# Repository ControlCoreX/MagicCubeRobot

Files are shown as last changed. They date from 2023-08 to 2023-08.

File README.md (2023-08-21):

# MagicCubeRobot
自己做的一个全自动解魔方装置. (下了大力气, 花了大价钱)

我的邮箱地址: TwithZ@163.com, 欢迎讨论交流!

演示视频地址: [演示视频](https://www.bilibili.com/video/BV1zj411979p/?vd_source=939818502857687a4a334c7a40d2c98a).

## 1. 整体简介
这是我做的第一个完整度较高的项目, 整体分为3个部分: 上位机, 下位机, 机械结构.
1. 上位机: (树莓派+上位机)
   1. 使用的技术: 树莓派4B(8GB); 使用opencv进行图像处理; 全部使用C++语言编写; 使用g++编译器构建; 使用CMake工具管理工程; 使用git进行版本控制; 使用POSIX pthread线程库进行多线程设计; 使用了WiringPi库控制串口(但实际大多是使用的都是Linux的系统调用进行数据读写); 没有使用GUI, 采用了CLI的方式与用户交互(虽然但是, 经过我的设计, 操作起来也非常方便); 还用Qt编写了一个上位机(仅用于中继, 它的功能后面会介绍), 其中使用了winsocket进行本机网络通信.
   2. 负责的功能: 负责与用户的交互, 图像的采集, 魔方描述字符串的生成, 与开源解魔方软件网络通信, 与下位机通信.
2. 下位机:
   1. 使用的技术: STM32F407+FreeRTOS.
   2. 负责的功能: 接收上位机传来的指令, 并控制步进电机运动.
3. 机械部分: SolidWorks, 零件都是在网上加工的, 使用的材料有CNC铝加工(只用了一小点, 奈何实在是太贵了), 3D打印树脂, 尼龙, 亚克力板, 不锈钢冲压工艺. (后面这些都是妥协的. 由于第一次做机加工这种事, 前期没有料想到CNC铝加工这么贵, 所以最开始计划的是全部都是用CNC, 后来发现太贵了, 才一点一点妥协, 从铝变成了3D打印塑料, 变成了冲压的不锈钢, 变成了亚克力板. 不过我感觉这也是一个成长过程吧, 以后做产品的话, 在机加工这方面也肯定是要根据成本来选择加工工艺的啊)

## 2. 软件架构介绍
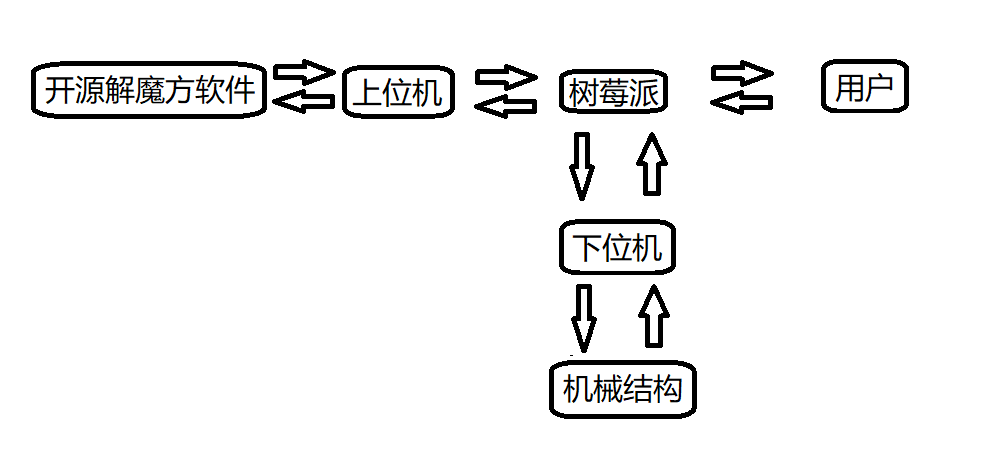
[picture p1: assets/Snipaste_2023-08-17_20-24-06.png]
整体架构图

**1. 架构图说明**: 整体架构关系图如上图所示, 在操作过程中, 用户只需要通过鼠标键盘与树莓派进行交互就可以了, 极大简化了操作, 在设计时我是有意设置成这样的, 用户完全不用操作STM32, <u>我相当于把STM32当做了树莓派的一个从设备.</u> 系统上电之后(就只有一个开关), 用户所需做的就是操作鼠标和键盘. 用户把需要的动作以指令的形式输入给树莓派, 树莓派会将会根据指令控制STM32, 进而控制机械机构来执行对应动作.

**2. 工作流程**: 系统初始化 > 树莓派采集图像 > 通过算法识别出魔方6个面, 共计54个色块的颜色 > 树莓派根据颜色生成描述魔方色块和方位信息的字符串 > 将字符串通过串口发送给上位机 > 上位机通过网络将该字符串发送给开源解魔方软件, 该软件会自动给出魔方还原步骤, 并返回给上位机 > 上位机将还原步骤发送给树莓派 > 树莓派将还原步骤发送给下位机 > 下位机根据还原步骤解析生成实际控制电机的结构体数组 > STM32控制机械结构全自动完成魔方还原.

**3. 上位机软件设计**: 使用树莓派4B, 采用POSIX多线程. 使用opencv进行图像处理和颜色识别. 下面只讲几个比较重要的点吧.
1. 实时识别. 颜色识别是在视频流中直接识别的, 而不是先拍摄图像, 后进行识别. 这样反馈通路的延迟小, 便于快速获得识别结果. 程序在视频流中直接显示识别结果, 当识别结果正确时, 用户只需要敲一下键盘即可去识别魔方的下一个面.
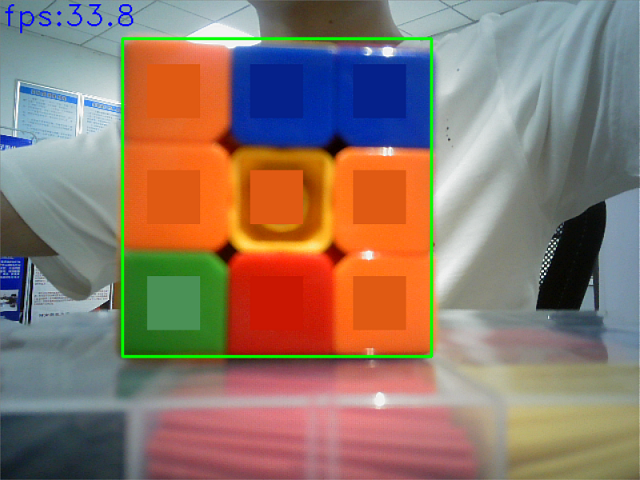
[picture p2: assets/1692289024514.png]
实时识别
   
2. 颜色识别算法在**BGR色彩空间**中完成, 使用颜色距离来判断两种颜色的接近程度, 从而判断出目标色块的颜色. 因为一种彩色有BGR共3个通道, 也就是3个分量, 如果分别以BGR3个分量为坐标轴, 那么它们所能形成的所有颜色, 在空间中就可以形成一个处于第一卦限的正方体(离散的). 那么以这种视角, 每一种颜色在空间中也就是一个点, 那么两种颜色的接近程度就可以用这两个点之间的距离来衡量, 距离近表示两种颜色很接近, 距离远表示两种颜色差异很大. (注: 这里这种距离我使用的是欧氏距离, 具体原因我目前无法解释, 但是效果很好; 还有一种距离叫曼哈顿距离, 我没有试, 不知道效果会怎么样). 公式如下:
公式
3. 在图像领域一个非常影响软件性能的因素就是光照, 在这个项目的颜色识别中也不例外, 我在设计中非常要注意的一个点就是对于光照的抗干扰能力要强. 为此我设计了一个debug线程, 专门用于调整bgr的阈值, 因为识别颜色主要就靠这些阈值来进行的. 不同于一般的手动调整阈值的方法, 我在设计时着重考虑了易用性, 即**用户友好性friendly**. 当某个颜色识别不准确时, 只需按下一个键便会自动创建一个debug线程, 然后在这里用户只需要手动指定一下识别不准确的颜色, 然后程序会自动计算该处的bgr值, 然后以计算得到的值来作为阈值. (实际测试, 这种方法效果很好)
4. 设计实现了一个功能类似shell的软件. 实现的效果为: 用户可以在树莓派的terminal中输入一个函数名, 并带上参数, 然后回车, 单片机上就可以执行同名的函数, 并使用在terminal输入的参数(且参数可定制, 默认支持3个参数). 即我可以在单片机运行时手动让其执行某个函数. 这种设计非常方便调试!!! (还有种**分布式**的概念在里面, 树莓派上的线程, 单片机上的线程, 都当做是同等的线程, 只不过是跑在不同的设备上的而已, 我在用的时候直接就把单片机上的线程当做了树莓派上的线程, 因为使用起来在用户看来没什么两样, 中间那一层对用户来说是**透明的**)

**4. 下位机软件设计**: 采用了FreeRTOS实时操作系统, 采用多线程设计, 在软件编写上比裸机要更容易一些. 在该项目中我共使用了4个线程, 分别是: LED状态灯线程`status_led_task`, 限位开关扫描线程`limit_task`, 命令处理线程`cmd_proc_task`, 数据处理线程`data_proc_task`.
1. LED状态灯线程就是用于控制指示灯的亮灭(线程的优先级很低). 在实际产品中, 指示灯的设置非常重要, 它可以用于判断系统是否工作正常, 对于软件调试非常重要.
2. 限位开关扫描线程, 它就是用于扫描限位开关状态的, 因为使用的是步进电机, 并不是闭环的伺服电机, 所以需要使用限位开关来设定初始位置, 再假定步进电机不丢步, 近似认为其是一个闭环系统. 本项目中限位开关的扫描频率为100Hz(最大为), 周期10ms, 要根据滑轨的速度来调节该扫描频率, 过快浪费系统资源, 过慢起不到效果.
3. 命令处理线程和数据处理线程, 在树莓派中我设计了两个程序, 一个是主要的程序, 用于图像识别和解魔方, 还有一个程序时专门用于调试的, 其位置在`./树莓派部分/MagicCubeRobot/manual_mode`文件夹下, 见名知意, 即手动模式, 也就是说用户可以通过键盘来控制机械结构的运动, 它跟用于图像识别的程序对STM32的控制是独立的, 所以我在这里就设计了两个线程来分别接收这两个程序对STM32的控制, 但是使用的是同一套通信协议(这个后面讲), 数据处理线程用于处理图像识别程序发来的数据, 命令处理线程用于处理手动控制程序发来的数据. 下面讲一下实现细节:
   - 由于通过树莓派发来的数据都并非是单个字节的, 而是很大一长串, 而且数据的长度还是不确定的(如魔方还原步骤的长短可能不同), 所以这就涉及到串口不定长数据的接收, 关于不定长数据的接收有很多方式, 其中正点原子的方式我感觉不是很好, 至少不是专业的方法, 它是用串口接收中断, 来一个字节就接收一个字节, 最后拼到一块. 我觉得这种方法有一个很大的缺点就是浪费资源, 因为用的是接收中断, 那如果接收的字节数非常多, 那就要中断很多次, 而且中断频率也是很高的, 因为来一个字节就要接收一次(如果波特率是115200的话, 中断频率是可以计算出来的), 而我采用的又是RTOS, 调度器才1ms中断一次, 这导致了在接收数据时, 大部分时间单片机都卡在串口接收中断里, 这很不专业. 所以我觉得这种使用串口接收中断来接收不定长数据的方式只适合做简单的应用, 不适合正规生产中. 在这里我使用的是**串口空闲中断+DMA**的方式, 这种方式高效, 不需要CPU参与数据搬运.
   - 由于数据有两个用途: 数据或命令. 所以我需要在数据包中有一个标识符来标记这个数据包是数据还是命令. 为此我设计了一个协议格式. 如下:
     ```c
     typedef struct
     {
          uint8_t  head;//!< 帧头
	      uint8_t  type;//!< 类型标识符
	      uint16_t len;//!< 数据长度
	      uint8_t  data[USART2_DMA_RECV_BUF_SIZE - 4U];//!< 数据域
     }pack_t;
     ```
     树莓派上的两个程序在向单片机发送数据时都使用这种数据包, 所以单片机就可以根据type成员来判断接收到的是数据还是命令, 从而对数据进行不同的解析, 交给不同的线程去处理.
   - 单片机串口空闲中断接收到一个数据包中断一次, 然后通过type成员执行不同的操作, 进而唤醒不同的线程(当没有接收到数据时, 对应的线程都是阻塞状态的), 进行不同的处理.
   - 还有一些别的细节, 如两种数据的种类是不一样的, 命令时数据类型是`uint32_t`型的, 而数据时数据类型是`uint8_t`类型的, 为了方便, 我在设计时将数据传输流规定为了使字节流, 所以如果传输的是命令, 还要根据机器的**大小端**进行4个byte拼接为一个`uint32_t`.

**5. 一些软件设计细节!!!**: (代码强迫症...)
1. 代码命名规范. 命名使用Unix的风格, 即全部小写, 以下划线分隔; 对于常用单词的缩写也有规定, 对于同一个单词, 不允许使用不同的缩写. 比如length缩写就为len, command的缩写久违cmd, 所有地方都保持统一. 这种做法有人可能认为是强迫症, 但我认为"不乱起名", "名称保持统一"在软件开发中是一个好习惯, 不至于引起迷惑!!!
2. 注释规范. (符合doxygen注释规范, 便于自动生成文档)
   ```c
   //! 单行行首注释.
   func_bar();//!< 单行行尾注释.
   /*!
    * 多行注释.
    * 多行注释.
    */
3. Terminal中输出的信息为彩色, 不同level的log用不同颜色的输出表示. 典型的就是绿色表示成功, 红色表示失败. 我还使用了蓝色表示较为重要的提示.
4. 统统采用多线程设计. 我觉得这应该是以后的主流, 裸跑不太好.

## 3. 硬件部分
这一部分就只是设计了一个转接板, 主要是为了方便连线, 不让走线太凌乱, 因为一共使用了11个步进电机, 1个舵机, 4个限位开关, 一共大约是125根线, 如果都直接连到核心板上多少有点难看, 而且还不稳定, 再者我要以做产品的标准来要求自己, 所以我弄了一个转接板, 通过接线端子来吧这些线引出去, 最终效果很好, 也没有显得很凌乱.
![转接板图片](./assets/1692288660302.jpg)

## 4. 机械部分
![3维模型](./assets/1692289251094.jpg)
这一部分也是我在这个项目中花费精力最大的一部分, 由于之前没有做过机加工的经验, SolidWorks也是现学现卖, 对于很多东西都不懂, 中间也踩了很多坑, 在这里感谢实验室王老师的资金支持!!!

在设计机械机构使我的主要目标就是要实现全自动, 之前一代解魔方机器是使用了4个摄像头, 这里我设计了一套机械装置实现了仅使用一个摄像头就可以实现对魔方6个面的图像采集. 如上图中红圈中的结构.

为了保证水平方向4个拧手在向中心运动时的一致性, 我还设计了一套联动机构, 通过同步轮和同步带实现水平方向4个电机同时到达中心位置.

总之吧, 在设计上我注意了很多细节, 这里就不一一说了, 说多了都是泪......

---

2023年8月18日00:31:47

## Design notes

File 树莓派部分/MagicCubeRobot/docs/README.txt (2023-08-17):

约定:
    通道顺序使用bgr, 而非rgb. 在命名中也使用了bgr.
    对于那种可以使用一维数组, 也可以用二维数组表示的数据. 约定:
        如果选择用一维数组来表示, 则数组名使用复数.
        如果选择用二维数组来表示, 则数组名使用单数.
    一共分为3个线程:
        1. 进行色块识别的线程叫 video thread.
        2. 获取各种颜色的bgr值得线程叫 debug thread.
        3. 与下位机进行通信的线程叫 com thread.
    标记都用绿色.
    
由于很多情况下, 对象都并非单纯的变量, 那么通过函数返回值返回这种对象就比较不方便.
另外为了形式上的统一, 规定: 尽量让函数的返回值都是void, 数据的传入和传出都通过参数完成.
而且对于需要传出数据的参数, 使用"引用"的语法, 而不适用"指针"的语法.

关于函数形参的顺序的约定: 传入参数在前, 传出参数在后.

在终端中的提示的颜色:
    错误: 红色加粗
    成功: 绿色加粗
    一般提示: 白色加粗.
    稍重要提示: 蓝色加粗.

命名规范:
    calculate 简写为 calc
    sample    简写为 samp

名词解释:
    roi表示的是摄像头拍到的画面中, 魔方所在的区域, 认为是roi.
    samp表示的是判定颜色时, 参与计算的区域.

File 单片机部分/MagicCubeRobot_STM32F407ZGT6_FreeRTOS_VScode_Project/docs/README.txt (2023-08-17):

/*!
 * @file: README.txt
 * @author: 屠文博-自卓201-201404010126
 * @date: 2023年5月17日20:53:26
 * @brief:  1. 一些硬件资源分配信息.
 *          2. 注意事项.
 *          3. 一些规范.
 */

解魔方机器人单片机端资源分配(2023年4月4日16:17:47)

控制步进电机使用 TIM3, CH1, PA6
DMA使用的是 USART2, PA2, PA3
控制舵机使用 TIM4, CH1, PD12

有一个控制步进电机使能与否的按钮, 因为使能, 所有电机可以同时使能, 同时失能, 要是所有11
个电机全部都用一个引脚控制的话, 那得很多引脚, 鉴于此, 直接用地线和vcc来控制使能失能.
而方向引脚每个电机用一个引脚控制.

步进电机的方向表示, 0表示顺时针, 1表示逆时针.
大部分电机的细分调的都是400个脉冲转一圈. 有些因为速度或其他的原因不是这样的.
单片机每秒产生800个脉冲. 如果是400个一圈的话, 则转速就是1秒转2圈.

一个函数前加了static表示这个函数只希望在本文件中使用, 不需要在外部使用. 类似文件私有的函数.

注释采用Doxygen规范:
    单行注释:   1. 该行中仅有注释:
                    //! 这是注释.
                    this is code;

                2. 在代码后注释:
                    this is code;//!< 这是注释.
    多行注释:   /*!
                * 1. this is comment.
                * 2. this is comment.
                * 3. this is comment.
                */

这是一个vscode工程, 需要先搭建一下vscode开发STM32的环境.

在注释中线程跟任务不作区分.

单词的缩写标准跟上位机一样.

编译程序只需要在命令行里输入make命令并回车即可.
下载程序只需要在命令行里输入make download命令并回车即可. (下载程序时一般第一次下不进去, 这时候拔插一下ST-Link再下就能下进去了. 我也不知道为啥, 还没有去认真解决它)

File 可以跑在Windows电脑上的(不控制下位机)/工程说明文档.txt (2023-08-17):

就跟建VS的opencv工程差不多, 先建一个opencv的工程, 这里面用的opencv3.4.2
因为要用网络通信, 需要在附加依赖项中多加一个ws2_32.lib
因为使用了winsocket和opencv, 里面的命名空间有干扰, 如果不做处理的话, 编译会报错
说"ACCESS_MASK"不明确符号, 这时候需要把"using namespace cv;"这一句给去掉,
然后把所有cv命令空间的东西, 使用cv::这种方式搞一下, 然后就不报错了.

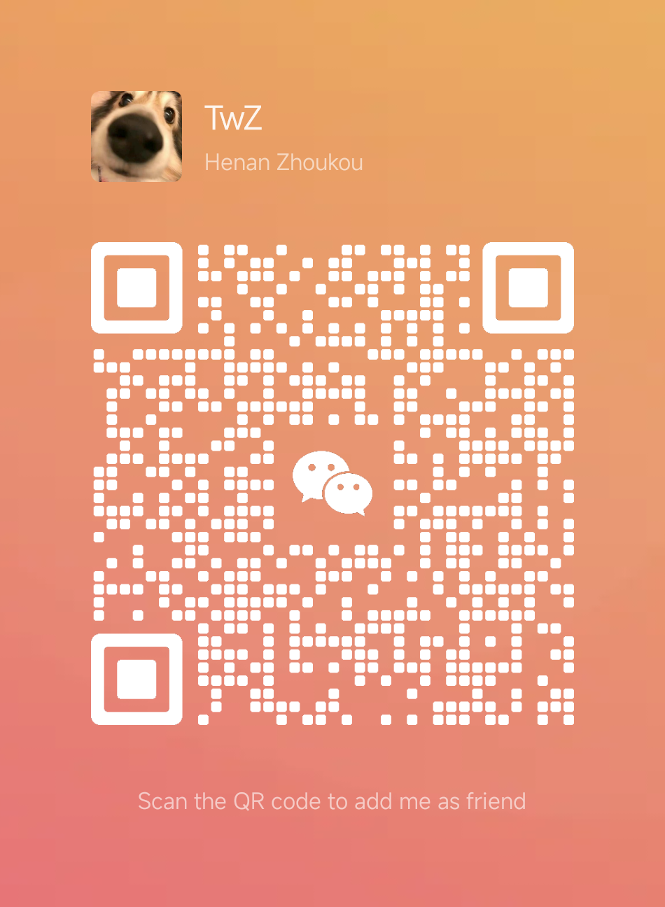
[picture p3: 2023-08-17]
assets/wechat.png

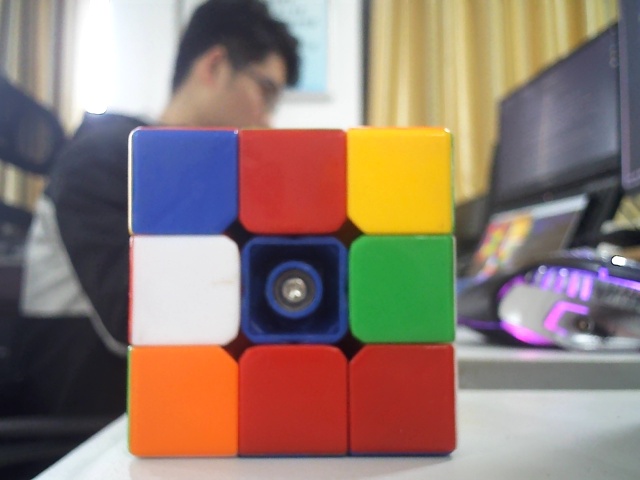
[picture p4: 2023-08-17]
树莓派部分/MagicCubeRobot/picture/six-color.jpg

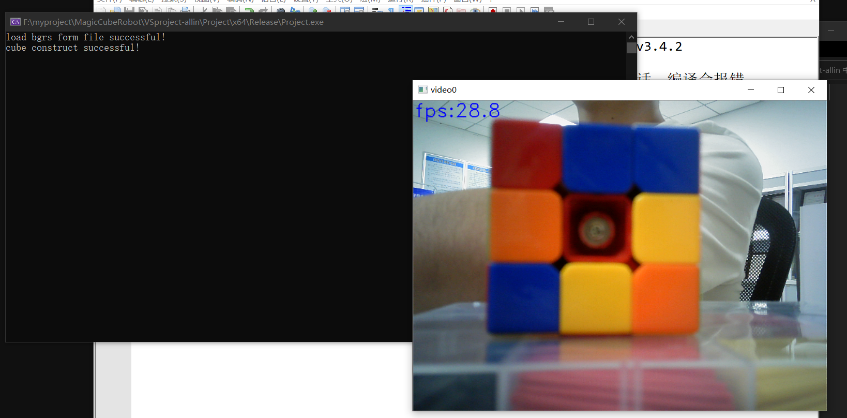
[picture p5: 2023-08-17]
可以跑在Windows电脑上的(不控制下位机)/示例图片/Snipaste_2023-06-06_16-59-30.png

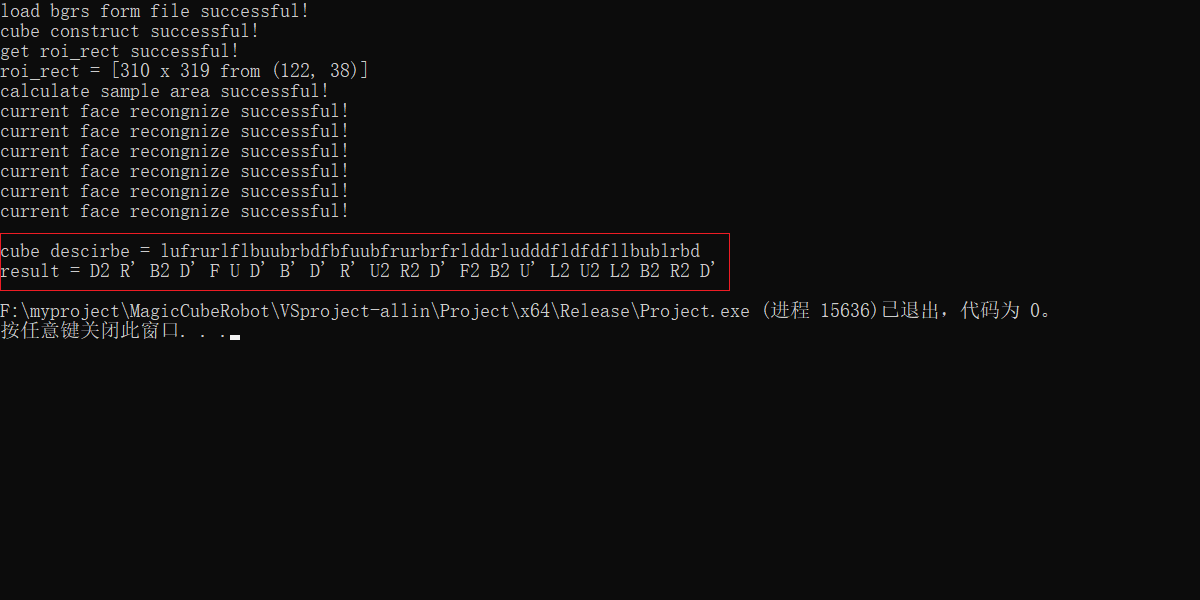
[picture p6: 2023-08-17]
可以跑在Windows电脑上的(不控制下位机)/示例图片/Snipaste_2023-06-06_17-02-21.png

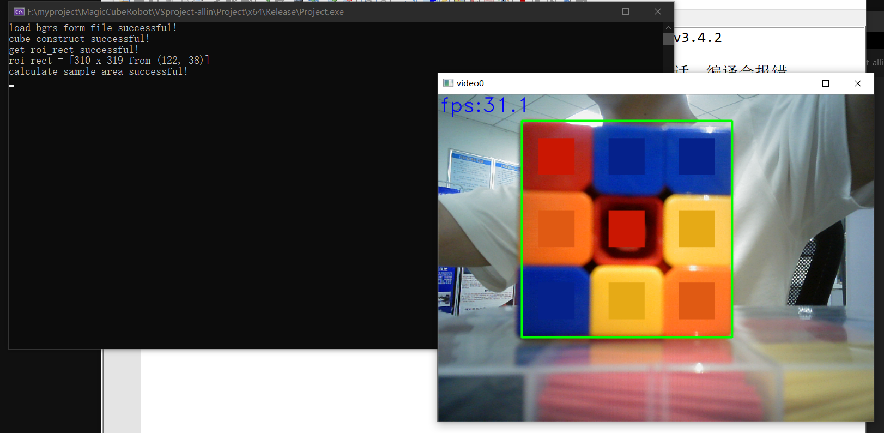
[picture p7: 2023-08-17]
可以跑在Windows电脑上的(不控制下位机)/示例图片/Snipaste_2023-06-06_17-00-23.png

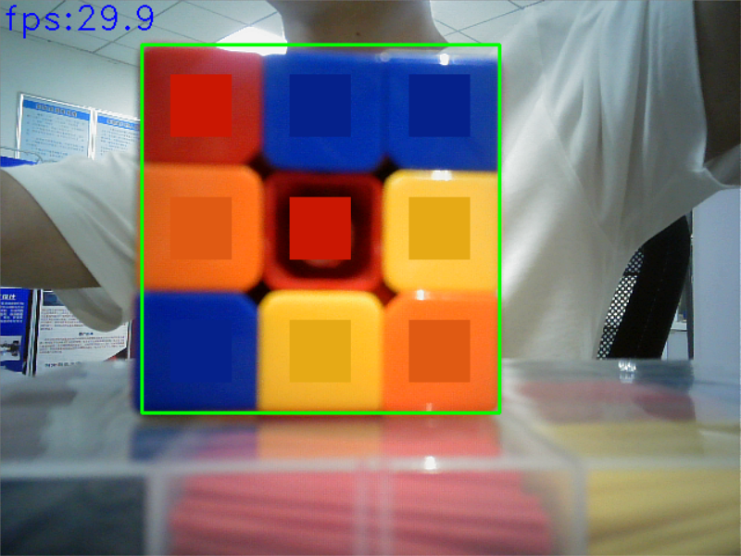
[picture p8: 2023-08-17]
可以跑在Windows电脑上的(不控制下位机)/示例图片/Snipaste_2023-06-06_17-00-09.png

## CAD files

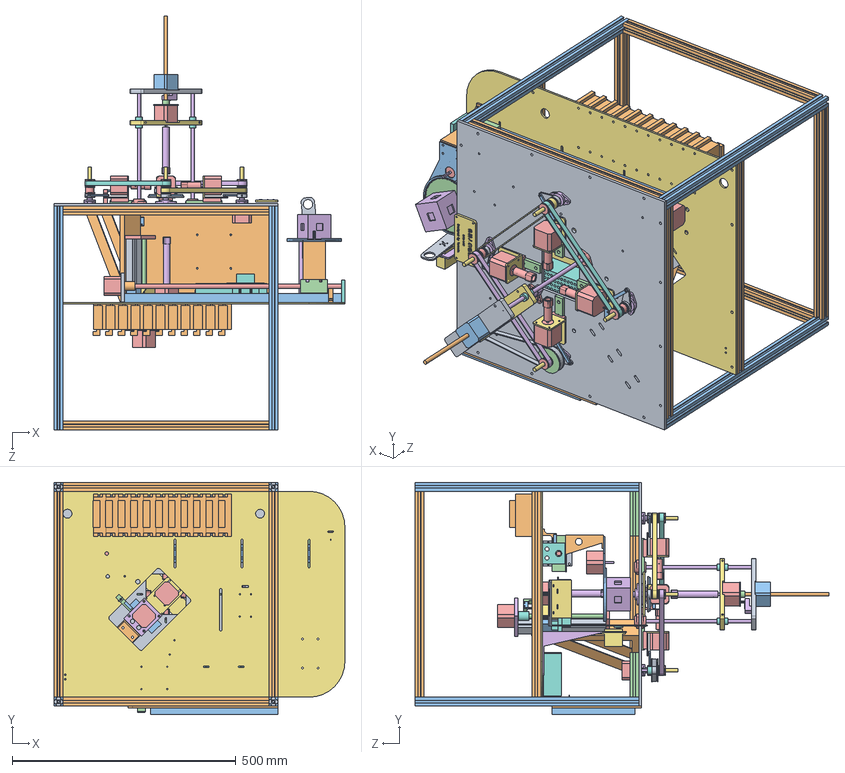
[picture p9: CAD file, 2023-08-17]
机械部分/最终装配结构-屠文博2023年4月5日.SLDASM
650.0 x 519.0 x 925.0 mm
上层平板
铝型材460mm x 9
铝型材500mm x 4
铝型材100mm x 2
端板从动端
端板电机端
加长步进电机座
联轴器
现有-滑轨
现有滑轨的固定架
现有-滑块
轴
42步进电机 x 10
42步进电机的轴 x 10
下层平板
端板从动端-超长
端板电机端-超长
联轴器超长
现有-滑轨-超长
现有-滑块-超长
轴-超长
摄像头立板
舵机
舵盘
摄像头曲柄
立板
水平支架
大齿轮
摄像头
魔方
42步进电机固定架 x 4
开关电源
树莓派4B
显示屏固定架
显示屏
滑轨 x 4
滑块 x 4
轴承座 x 8
8mm光轴-用于同步轮 x 4
42步进电机同步轮
摇杆 x 4
四方薄螺母 x 4
连杆 x 4
同步轮大
同步轮小 x 7
皮带6-7^最终装配结构-屠文博2023年4月5日
皮带7-8^最终装配结构-屠文博2023年4月5日
皮带8-9^最终装配结构-屠文博2023年4月5日
皮带9-10^最终装配结构-屠文博2023年4月5日
步进电机驱动器 x 11
船形开关
使能开关
光轴固定座 x 4
8mm光轴 x 2
上部滑块
直线轴承 x 2
上部端块
8mm丝杆
贯穿式42丝杆步进电机
步进电机端盖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

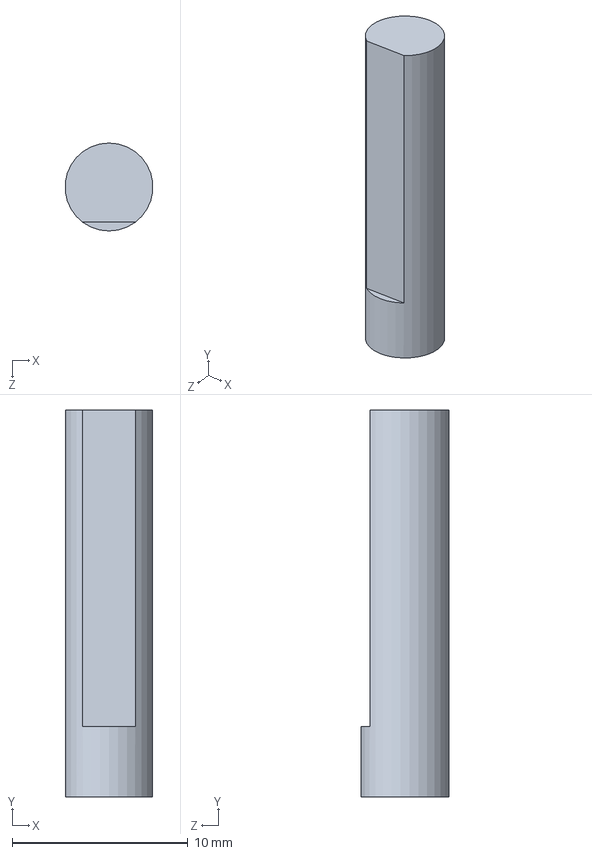
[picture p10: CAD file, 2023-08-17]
机械部分/42步进电机/42步进电机的轴.SLDPRT
4.97 x 22.0 x 5.00 mm

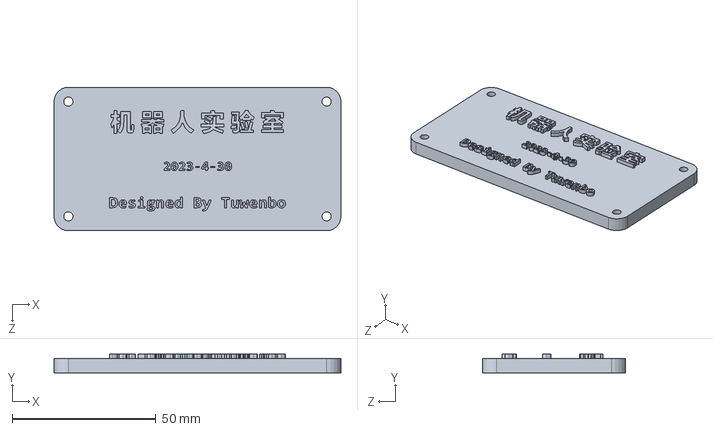
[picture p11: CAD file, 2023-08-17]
机械部分/mark/mark.SLDPRT
100.0 x 6.50 x 50.0 mm

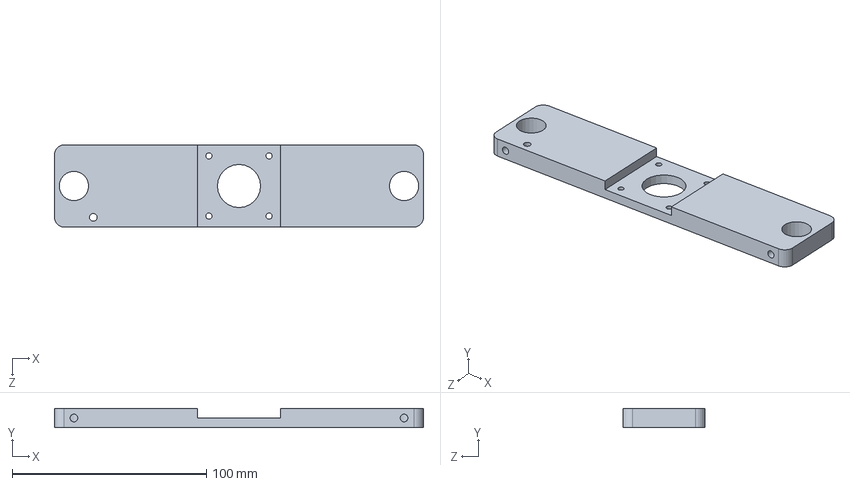
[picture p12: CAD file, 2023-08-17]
机械部分/上部导轨/上部滑块.SLDPRT
190.0 x 10.0 x 42.3 mm

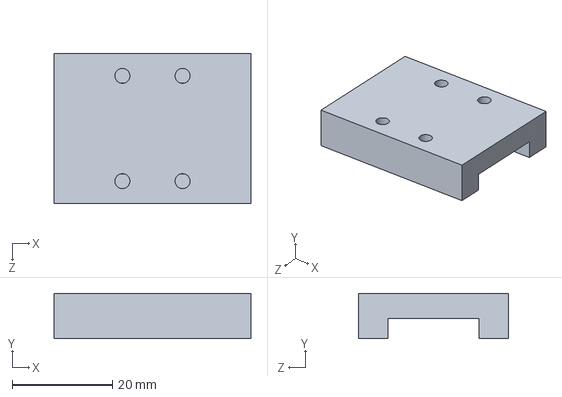
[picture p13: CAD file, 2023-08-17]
机械部分/小滑轨/滑块.SLDPRT
39.3 x 9.00 x 30.0 mm

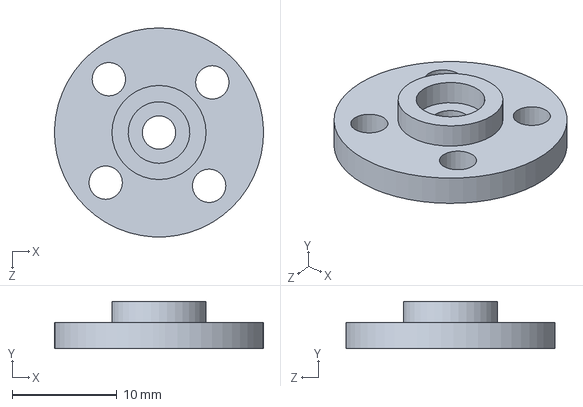
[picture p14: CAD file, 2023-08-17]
机械部分/支架/舵盘.SLDPRT
20.0 x 4.50 x 20.0 mm

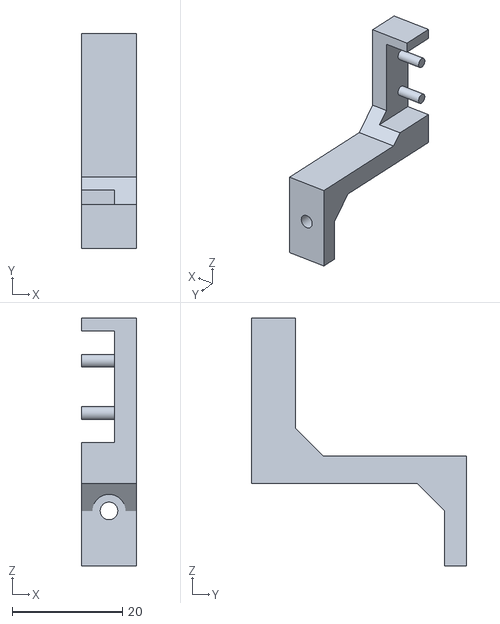
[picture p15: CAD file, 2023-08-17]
机械部分/最后一次加工/3D打印件/限位开关支架-下面导轨(要2个).STL
10.0 x 39.0 x 45.0

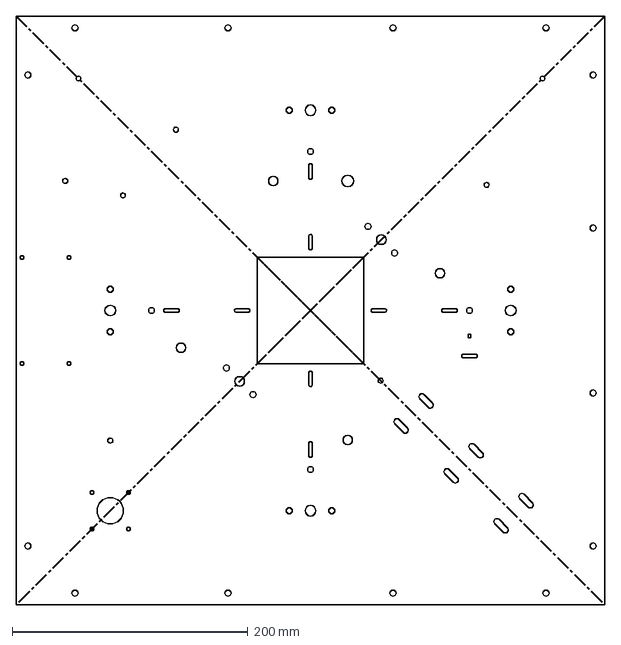
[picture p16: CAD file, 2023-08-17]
机械部分/最后一次加工/亚克力板/上层平板(要1块).DXF
500.0 x 500.0 mm

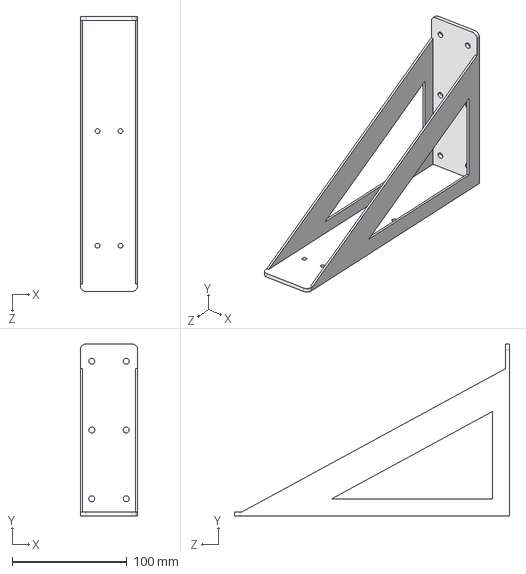
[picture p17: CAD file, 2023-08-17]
机械部分/最后一次加工/冲压件/现有滑轨的固定架(要1个).STEP
50.0 x 150.0 x 240.0 mm

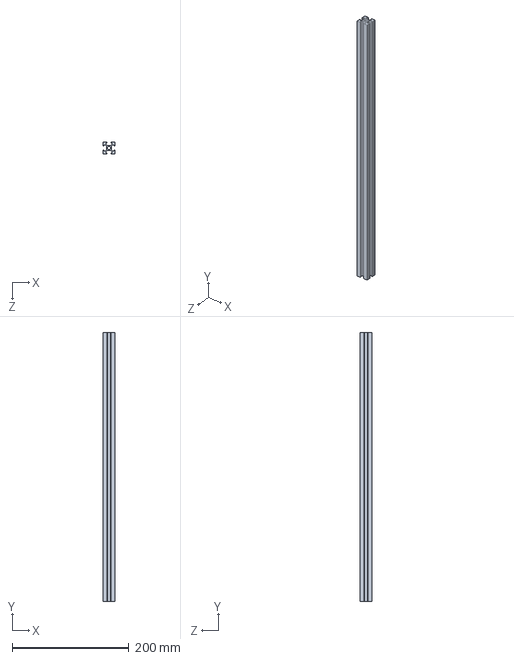
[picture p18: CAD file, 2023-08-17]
机械部分/欧标2020铝型材/铝型材460mm.SLDPRT
20.0 x 460.0 x 20.0 mm

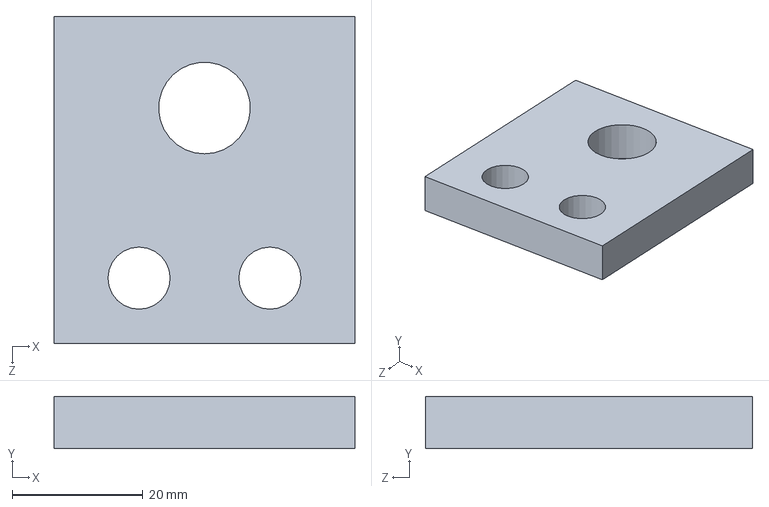
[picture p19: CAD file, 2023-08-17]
机械部分/现有的电动直线滑轨-超长/端板从动端-超长.SLDPRT
46.0 x 8.00 x 50.0 mm

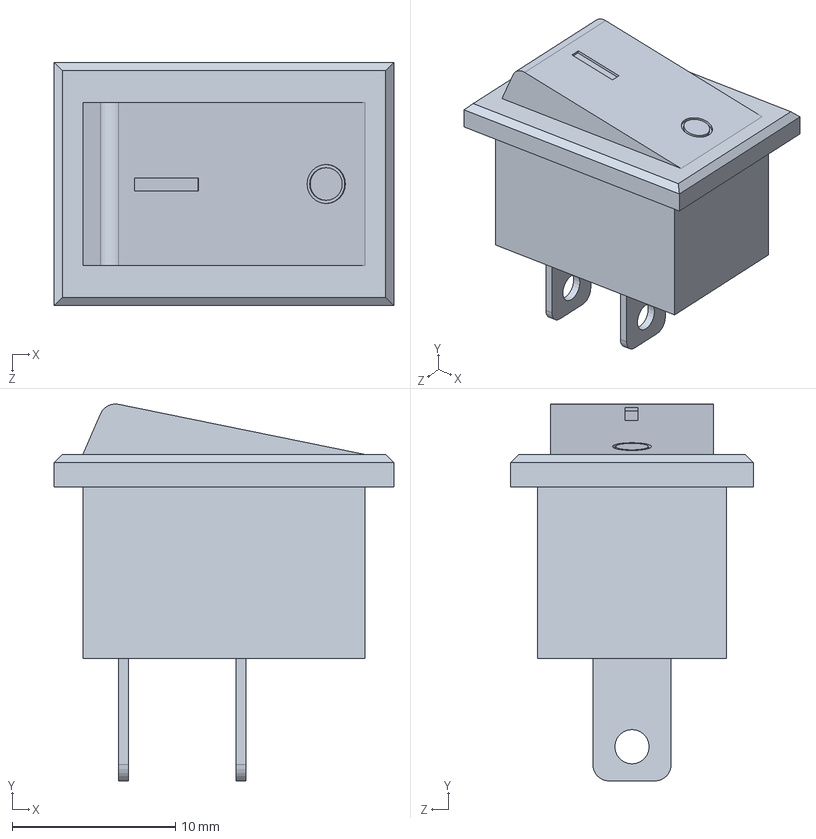
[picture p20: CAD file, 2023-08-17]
机械部分/船形开关.SLDPRT
20.8 x 23.1 x 14.9 mm

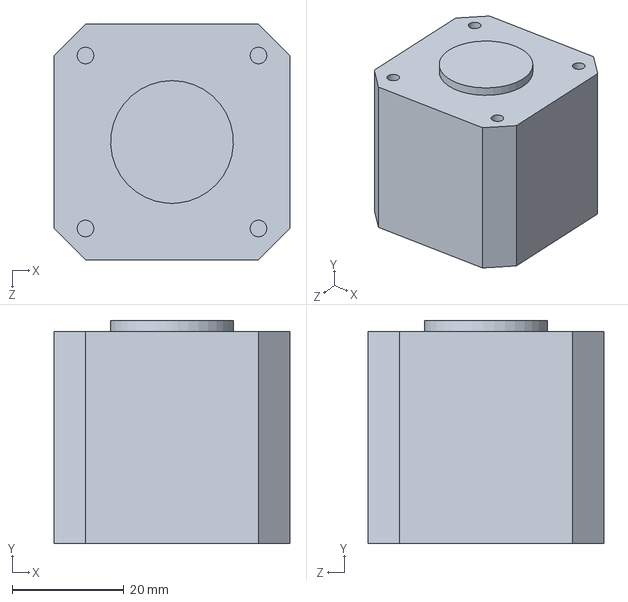
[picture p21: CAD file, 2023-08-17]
机械部分/42步进电机/42步进电机.SLDPRT
42.3 x 40.0 x 42.3 mm

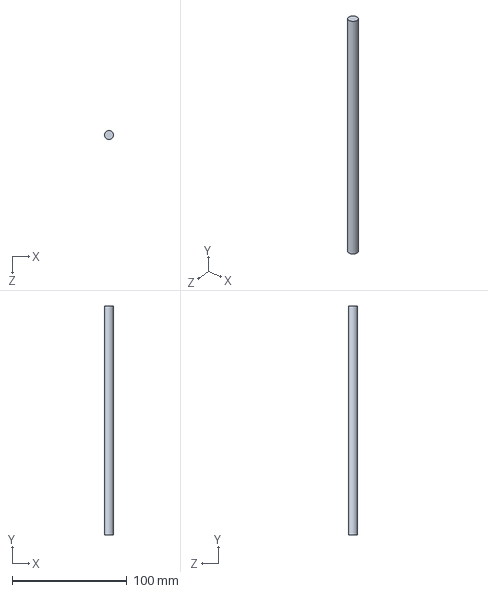
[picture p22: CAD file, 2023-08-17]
机械部分/上部导轨/8mm丝杆.SLDPRT
8.00 x 200.0 x 8.00 mm

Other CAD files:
机械部分/现有的电动直线滑轨/现有滑轨的固定架.SLDPRT
机械部分/同步轮大.SLDPRT
机械部分/小滑轨/滑轨.SLDPRT
机械部分/支架/水平支架.SLDPRT
机械部分/35mm铜柱.SLDPRT
机械部分/42步进电机/42步进电机同步轮.SLDPRT
机械部分/42步进电机/42步进电机固定架.SLDPRT
机械部分/8mm光轴-用于同步轮.SLDPRT
机械部分/上层平板.SLDPRT
机械部分/上部导轨/8mm光轴.SLDPRT
机械部分/上部导轨/上部端块.SLDPRT
机械部分/上部导轨/光轴固定座.SLDPRT
机械部分/上部导轨/步进电机端盖.SLDPRT
机械部分/上部导轨/直线轴承.SLDPRT
机械部分/上部导轨/贯穿式42丝杆步进电机.SLDPRT
机械部分/下层平板.SLDPRT
机械部分/使能开关.SLDPRT
机械部分/同步轮小.SLDPRT
机械部分/四方薄螺母.SLDPRT
机械部分/开关电源.SLDPRT
机械部分/摄像头.SLDPRT
机械部分/摄像头座.SLDPRT
机械部分/摇杆.SLDPRT
机械部分/支架/大齿轮.SLDPRT
机械部分/支架/小齿轮.SLDPRT
机械部分/支架/摄像头曲柄.SLDPRT
机械部分/支架/摄像头立板.SLDPRT
机械部分/支架/立板.SLDPRT
机械部分/支架/舵机.SLDPRT
机械部分/支架/魔方.SLDPRT
机械部分/显示屏.SLDPRT
机械部分/显示屏固定架.SLDPRT
机械部分/最后一次加工/3D打印件/mark(要2个).STL
机械部分/最后一次加工/3D打印件/大齿轮(要1个).STL
机械部分/最后一次加工/3D打印件/摄像头座(要1个).STL
机械部分/最后一次加工/3D打印件/限位开关支架-上部导轨(要2个).STL
机械部分/最后一次加工/3D打印件/限位开关支架-水平导轨(要2个).STL
机械部分/最后一次加工/3D打印件/限位开关支架-长导轨(要2个).STL
机械部分/最后一次加工/亚克力板/下层平板(要1块).DXF
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

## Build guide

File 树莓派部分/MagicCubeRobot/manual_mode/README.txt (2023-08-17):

这个文件中的文件是用于手动调试的.
如果不需要用到此功能, 那就不必编译它, 所以把这个功能设计成了跟主功能分开的形式.
这是一个独立的可执行文件, 它需要独立编译, 因为这个比较简单, 所以没有提供Makefile, 在命令行编译就行.
编译命令为: gcc manual.c ../tucomm/tucomm.c -o manual -lwiringPi -I.. -I../tucomm

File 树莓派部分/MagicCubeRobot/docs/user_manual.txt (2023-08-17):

使用方法:

录制一个 使用方法 和 代码架构 讲解的视频.

可以给它加一个急停按钮.

在每个文件中都写一段描述这个文件作用的说明.

树莓派上的两个串口, 该怎么连接, 引脚在哪.

同志你为我的这个项目打多少分? (10分制)

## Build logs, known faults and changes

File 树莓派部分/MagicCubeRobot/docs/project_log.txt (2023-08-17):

** 解魔方机器人项目日志 **

项目名称: 解魔方机器人
项目作者: 屠文博
起始日期: 2022年11月4日

==========================

2022-11-10-16:57 ->
	重构, 马德之前写的给弄丢了, 没备份好, 现在写着贼烦.
	昨天晚上以为都写好了, 就剩下查bug了, 结果今天早上一来就发现, 写的不行, 还得特么重新写.
	得换一个方法. 换成实时识别的, 他识别对了, 用户在手动给出指令让识别下一个面.
	这样好调试啊! 唉...无奈

2022-11-14-20:49 ->
	马的, 今天晚上本来想加一个调试宏TU_INFO的, 鬼知道为啥,它给我报一大堆莫名其妙的错误.
	艹!

2022-11-15-11:42 ->
	今天上午找bug找了一上午, 终于把那个segmentfault的bug给找出来了, 挺开心, 一上午没白忙!
	但是现在颜色还是识别不对啊! 应该后面还有类似的Bug, 得一点一点的调了啊!
	唉...真操蛋...

2022-11-15-19:07 ->
	又打算重构了!!!
	之前的方法, 直接在代码中把各个颜色的h, s, v值写死了, 有点不好, 感觉h这个值从0~180分的等级有点少了, 
	容易识别错误, 对于用手调来说很好用, 但是这种算法里自动识别的,不是那么好用.
	所以接下来我想把手动调节, 获得各个颜色的hsv值得程序给加进去, 这样只要愿意调, 颜色总能识别正确的, 
	就不会存在识别错误的情况了, 也不用像前几代那样还要补光啥的.
	为了后续的扩展性, 也为了练习一下我刚学的进程间通信, 多线程的知识, 我想用一下多进程和多线程!
	总体结构就是: 启动之后就先启动另一个进程让用户调节, 获取各种颜色的hsv值, 至于把调节到的hsv值, 
	则通过进程间通信的方式传回来.

2022-11-20-11:35 ->
	又打算重构了!!!
	用上一种方法, 本来以为效果会挺好的, 但实际做出来, 发现那写轮廓要找起来还是挺麻烦的, 杂点太多了.
	昨天我问了一下李勋老师, 他给了我一点建议. 我打算用RGB试试了, 之前一直在HSV下做的, 效果一直不咋好, 
	RGB里还一直没试过.
	我打算不再弄什么采样区域边长了, 直接计算整个面的平均值, 也先不设置步长, 先看看速度咋样吧.
	这样整个求平均值, 那其实就跟人眼看起来是一样的了, 既然人眼能识别出来颜色, 那按道理来说, 机器也肯定能识别出来!
	要在RGB色彩空间下计算一下颜色之间的距离.
	唉...一遍又一遍地重写, 人都给我写麻了...

2023-1-8-16:29 ->
	诶...耽误了一段时间, 闲言少叙, 开始干吧!
	哦对! 我这是没有用vim, 用了vscode里的ssh插件, 用vscode写代码舒服一点.

2023-1-8-17:08 ->
	得一步一步的弄了, 要想判定颜色, 我得先知道每种颜色的bgr值分别是多少啊!
	所以我得先完成debug下的任务. 然后再往下做.

2023-1-9-16:57 ->
	今天该了好多东西, 还挺有收获嘞!
	把计算一个方块的bgr的平均值的函数给调试好了!
	而且发现一个可好的调试方法, 就是你不知道参与计算的坐标对不对的话, 那就把
	那些坐标的点都设成黑色, 看是不是在你期望的位置就可以了!

2023-1-10-11:24 ->
	识别颜色终于算是弄好了! 艹!
	其实特么的也没有多难, 甚至可以说是简单. 但是之前就是一直没有弄出来...唉...
	我也没想到这种方法能这么好用, 识别正确率还挺高的!
	我还发现一个有意思的现象, 就是这种RGB色彩空间下, 识别颜色你在比较亮的环境中, 
	识别正确率挺高的, 但是在那种比较暗的环境中, 就很容易识别错. 
	所以后期继续做得话, 还是得补光!
	这应该也能推断出RGB色彩空间中, 各种颜色在3维空间中的分布情况!

	唉! 感触最深的就是: 我没想到这种方法的效果会这么好...
	之前一直在HSV上吃瘪...

2023-1-10-17:14 ->
	Makefile写的不是很会, 感觉应该没问题的, 它老是报错说头文件找不到...
	没办法, 今天下午我改用了CMake, 感觉也挺好用的.

2023-1-10-21:21 ->
	今天晚上把那些小细节都给该了该.
	想加读写文件那一部分嘞, 但是不知道为啥, 读写的时候总是不对, 真奇怪.
	以二进制方式读写方便一点.

2023-1-11-10:25 ->
	哎呀昨天晚上的那个bug找到了, 原来是我在打开文件的时候没有加权限...
	唉, 反正还是特么用的不熟...
	草了

2023-1-11-13:38 ->
	终于差不多了!
	图像识别部分已基本完工!
	瞌睡死了...

2023-1-18-19:51 ->
	前几天在弄网络那一部分, 也学了点, 在Ubuntu上也测试了, 也可以通信, 但是在树莓派跟
	电脑之间就是不行. 所以最后实在没办法, 就在电脑上用Qt写了个串口通信的东西, 来中继了
	一下. 这里还要感谢一下吴老板帮忙!
	这个做法实在是无奈之举, 网络部分我技术栈没有涉及到. 后续学弟可以把这一部分改进一下.

2023-1-19-15:01 ->
	把获取魔方解法的部分添加上吧!

2023-1-19-21:13 ->
	再做一次稍大的修改吧!
	之前的识别frame, 显示识别结果的部分, 这里用了一个index参数进行同步.
	但是仔细想想, 这个参数就很无脑, 你看函数说明的话就很难猜到这个参数是什么意思, 一点
	都不自然!
	而且这两个函数里面, 第一个进行识别, 识别一次就把识别结果写进去一次, 这很不应该, 肯定
	会降低效率!(确实, 没有进行识别的时候, 帧率在30fps~31fps, 进行识别之后就降到了28fps~
	28fps) 这种做法很傻啊! 应该是用户确认识别结果正确了, 再往里写, 而不应该每识别一次
	都写!
	所以我想改成: 取消index参数, 当用户手动确认识别正确之后, 再把结果写进去! 看看这次
	帧率会不会高一点点吧, 哈哈哈哈就算高也高不一点.

2023-1-20-1:01 ->
	终于弄好啦!!!
	颜色识别, 生成色块信息字符串, 获取解法, 都已经完成啦!!!
	真特么开心!!!
	弄了一晚上, 今晚都没陪郑郑聊天, 好想她!
	还是晚上比较有灵感, 今天白天坐在这就是写不出来, 烦死了!
	唉, 都凌晨了, 该碎觉了...
	大框架应该不会再改了, 只剩下一些细节上再优化优化了!

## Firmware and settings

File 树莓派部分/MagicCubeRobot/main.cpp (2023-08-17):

#include <wiringPi.h>
#include <wiringSerial.h>
#include <pthread.h>
#include <unistd.h>
#include <iostream>
#include <cstdio>
#include "colorful.h"
// #include "log.h"
#include "tucube.h"
#include "debug.h"
#include "tucomm.h"

using namespace std;


//! 因为在识别颜色的过程中需要转动魔方和摄像头, 这是控制转角的全局常量(没用宏).
const uint32_t STEP_CMD_INDEX = 1U;
const uint32_t SERVO_CMD_INDEX = 2U;

const uint32_t SERVO_POS_1_CMP = 47U;
const uint32_t SERVO_POS_2_CMP = 153U;
const uint32_t SERVO_POS_3_CMP = 245U;

uint32_t record_steps = 0U;//!< 记录步进电机转了多少个90°. 顺时针旋转+1, 不会逆时针旋转, 因为这里不包括手动模式时的转动.


//! 注意: 退出程序的时候, 把打开的所有文件都关闭掉!


int mcu_fd, inet_fd;//!< 串口文件描述符.
VideoCapture video;

pthread_t video_thread_tid;
pthread_t debug_thread_tid;
pthread_t com_thread_tid;

tucube cube(2U);//!< 定义一个对象.


void* video_thread_routine(void* param)
{
	Mat before_resize_frame, frame, frame_to_send;

	int posx = 0, posy = 0;//!< 用鼠标调整的坐标.
	
	Point roi_tl, roi_br;//!< ROI区域的左上角和右下角坐标.
	int roi_cnt = 0;//!< 记录本次选中的是ROI区域的第几个坐标.
	
	uint8_t mode = 0U;//!< 是在选择区域还是在拍照.
	const uint8_t CHOOSE_ROI_MODE = 0U, RECONGNIZE_COLOR_MODE = 1U;

	uint8_t index = 0U;//!< 拍照时图像的索引.

	char choice = 0;//!< 存储用户按下的键值.
	
	color_t colors[9];

	double ticks = 0.0, fps = 0.0;
	char fps_string[20];

	for( ; ; )
	{
		ticks = (double)getTickCount();

		video >> before_resize_frame;
		if(before_resize_frame.empty() == true)
			break;
		resize(before_resize_frame, frame, Size(640, 480));//!< 输入到对象中的图像是固定大小640×480, 不受摄像头的影响.
		
		choice = waitKey(25);
		
		if(mode == CHOOSE_ROI_MODE)
		{
			switch(choice)
			{
				case 'W':
				case 'w': 
					if(posy > 0) 
						posy -= 2;
					break;

				case 'K':
				case 'k': 
					if(posy > 0)
						posy -= 20;
					break;

				case 'S':
				case 's':
					posy += 2;
					break;

				case 'J':
				case 'j':
					posy += 20;
					break;

				case 'A':
				case 'a': 
					if(posx > 0)
						posx -= 2;
					break;

				case 'H':
				case 'h':
					if(posx > 0)
						posx -= 20;
					break;

				case 'D':
				case 'd':
					posx += 2;
					break;

				case 'L':
				case 'l':
					posx += 20;
					break;

				case 'N':
				case 'n':
					if(roi_cnt == 0)//!< ROI的左上角坐标确定好了.
					{
						//! 左上角坐标确定了, 就把左上角坐标存起来.
						roi_tl.x = posx;
						roi_tl.y = posy;

						roi_cnt++;//!< 标记要开始下一个点了.
						
						cout << COLOR_BOLD_GREEN "roi_rect tl is ok!" COLOR_OFF << endl;
					}	
					else
					{
						roi_br.x = posx + 5;
						roi_br.y = posy + 5;

						cout << COLOR_BOLD_GREEN "roi_rect br is ok!" COLOR_OFF << endl;

						cube.get_roi_from_user(Rect(roi_tl, roi_br));
						cube.calc_samp_area();//!< 开始计算采样点坐标.

						mode = RECONGNIZE_COLOR_MODE;//!< 进入实时识别模式. 

						//! 输出指示用户操作的信息.
						cout << COLOR_BOLD_BLUE "press 'N'/'n' to recongnize next face" << endl << \
												"press 'G'/'g' to debug" COLOR_OFF << endl;
					}
					break;
			}//!< end of 'switch(choice)'

			rectangle(frame, Rect(posx, posy, 5, 5), Scalar(0, 255, 0), -1);//!< 画出反馈点
		}//!< end of 'if(mode == CHOOSE_ROI_MODE)'
		else if(mode == RECONGNIZE_COLOR_MODE)
		{
			frame_to_send = frame.clone();

			rectangle(frame, cube.roi_rect, Scalar(0, 255, 0), 2);//!< 圈出ROI那个框.

			cube.recongnize_frame(frame, colors);//!< 识别当前帧.
			cube.show_recongnize_result(frame, colors);//!< 将识别结果显示到当前帧.

			//! 按下'n'键就把当前这个面的识别结果保存起来, 然后拍下一张.
			if(choice == 'N' || choice == 'n')
			{
				cube.store_recongnize_result(colors, index);//!< 识别结果存起来.

				cout << COLOR_BOLD_GREEN "current face recongnize successful!" COLOR_OFF << endl;//!< 提示识别成功.

				//! 舵机转动 或者 魔方转动, 这里还需要条件语句判断一下.
				switch(index)
				{
					case 0U://!< 如果识别的是第0个面, 那摄像头就转到位置2.
						tucomm_write_cmd(mcu_fd, SERVO_CMD_INDEX, SERVO_POS_2_CMP, 0U, 0U);//!< 舵机转到2位置.
						break;

					case 1U:
					case 2U:
					case 3U:
						tucomm_write_cmd(mcu_fd, STEP_CMD_INDEX, 0U, 1U, 377U);//!< 2, 3, 4的时候, 动作都是魔方旋转90度.
						record_steps += 1U;
						break;

					case 4U:
						tucomm_write_cmd(mcu_fd, STEP_CMD_INDEX, 0U, 1U, 377U);//!< 魔方旋转90度.
						record_steps += 1U;
						usleep(500000);//!< 此处休眠500ms, 因为这两句都要写文件, 如果间隔太短, 就会被当成是一个命令. (这里sleep会导致视频流卡住)
						tucomm_write_cmd(mcu_fd, SERVO_CMD_INDEX, SERVO_POS_3_CMP, 0U, 0U);//!< 舵机转到3位置
						break;
				}
			 	
				index++;

			 	if(index == 6U)//!< 6个面拍完了, 退出视频.
				{
					tucomm_write_cmd(mcu_fd, SERVO_CMD_INDEX, SERVO_POS_1_CMP, 0U, 0U);//!< 舵机归位.
			 		break;
				}

			}//!< end of 'if(choice == 'N' || choice == 'n')'
			else if(choice == 'G' || choice == 'g')//!< 发现颜色识别不对, 按'g'启动debug线程, 重新调整阈值.
			{
				pthread_create(&debug_thread_tid, NULL, debug_thread_routine, (void*)&frame_to_send);
				pthread_detach(debug_thread_tid);
				
				//! 重新开始识别6个面, 把index清零.
				index = 0U;
			}//!< end of 'else if(choice == 'G' || choice == 'g')'
		}//!< end of 'else if(mode == RECONGNIZE_COLOR_MODE)'

		//! 计算帧率并显示.
		fps = 1.0 / (((double)getTickCount() - ticks) / getTickFrequency());
		sprintf(fps_string, "fps:%.1lf", fps);
		putText(frame, fps_string, Point(2, 25), FONT_HERSHEY_DUPLEX, 1, Scalar(255, 0, 0), 1);

		imshow("video0", frame);

	}//!< end of 'for( ; ; )'

	video.release();//!< 释放视频流.
	destroyWindow("video0");

	cout << COLOR_BOLD_GREEN "six face recongnize successful!" COLOR_OFF << endl << endl;

	cout << COLOR_BOLD_BLUE "would like to see them:(y/n)" COLOR_OFF;//!< 查看识别结果.
	cin >> choice;
	if(choice == 'Y' || choice == 'y')
	{
		cube.show_final_recongnize_result('a');//!< 这里默认就用a方法, 因为b方法我没有写.
	}

	//! 生成描述魔方色块信息的字符串.
	cube.product_describe();
	printf(COLOR_BOLD_BLUE "\ncube descirbe = %s\n" COLOR_OFF, cube.describe);

	//! 将describe字符串发送给上位机, 获取魔方解法.
	write(inet_fd, cube.describe, 54);
	delay(1000);
	int slove_len = read(inet_fd, cube.slove, sizeof(cube.slove));//!< 读到的slove字符串中没有'\0'.
	if((slove_len != -1) && (cube.slove[0] != 'C'))//!< 这样才表示此魔方可解.
	{
		printf(COLOR_BOLD_BLUE "slove = %s\n" COLOR_OFF, cube.slove);//!< 把slove打印出来.
		tucomm_write_data(mcu_fd, slove_len, cube.slove);//!< 把slove发送给单片机. 单片机接收到要去解析.
	}
	else
	{
		printf(COLOR_BOLD_RED "get slove failed!\n" COLOR_OFF);
		exit(0);
	}

	exit(0);
}


//! 专门用来处理串口发来的指令的线程, 发一个指令, 这个线程置位一个标志位, 然后其它线程来处理.
//! 是否可以使用bitmap的方法.
void* com_thread_routine(void* param)
{
	int buf[10] = {0};
	uint16_t n = 0;

	for( ; ; )
	{
	//	tucom_read_data(fd, buf, &n);
		delay(3000);
	}

	return 0;
}


int main(int argc, char* argv[])
{
	if(wiringPiSetup() == -1)
	{
		cout << COLOR_BOLD_RED "wiringPi library open failed!" COLOR_OFF << endl;
		return -1;	
	}

	//! 打开与单片机通信的串口.
	mcu_fd = serialOpen("/dev/ttyAMA0", 115200);
	if(mcu_fd == -1)
	{
		cout << COLOR_BOLD_RED "mcu serial port open failed!" COLOR_OFF << endl;
		return -1;	
	}

	//! 打开与网络通信的串口. 这里使用uart2, 它对应的设备文件是/dev/ttyAMA1.
	inet_fd = serialOpen("/dev/ttyAMA1", 115200);
	if(inet_fd == -1)
	{
		cout << COLOR_BOLD_RED "inet serial port open failed!" COLOR_OFF << endl;
		return -1;	
	}

	//! open the camera.
	video.open(0);
	if(video.isOpened() == false)
	{
		cout << COLOR_BOLD_RED "video opened failed!" COLOR_OFF << endl;
		return -1;	
	}

	//! get the video's fps, because I want to clear the video buffer.	
	cout << "camera's fps = " << video.get(CAP_PROP_FPS) << endl;

	namedWindow("video0", WINDOW_AUTOSIZE);
	
	//! create the video thread.
    pthread_create(&video_thread_tid, NULL, video_thread_routine, NULL);	

	//! create the com thread.
//	pthread_create(&com_thread_tid, NULL, com_thread_routine, NULL);

	pthread_exit(NULL);
	return 0;
}

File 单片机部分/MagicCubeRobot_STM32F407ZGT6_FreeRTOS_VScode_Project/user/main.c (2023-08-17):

/*!
 * @file: main.c
 * @author: 屠文博-自卓201-201404010126
 * @date: 2023年5月17日20:51:07
 * @brief: 这也没什么好说的, 就是通过god_init()私有函数初始化全部硬件, 然后创建start_task, 在start_task里面创建所有任务.
 */

#include "delay.h"
#include "usart1.h"
#include "FreeRTOS.h"
#include "task.h"
#include "status_led.h"
#include "step_motor.h"
#include "servo.h"
#include "limit.h"
#include "usart2.h"
#include "tucomm.h"



static void god_init(void)
{
    delay_init();
    usart1_init(115200U);
    status_led_init();
    step_motor_init();
    servo_init();
    limit_gpio_config();
    usart2_dma_init();


}

int main(void)
{
    NVIC_PriorityGroupConfig(NVIC_PriorityGroup_4);
    god_init();

    extern void start_task_routine(void* param);
	static TaskHandle_t start_task_handle = NULL;

	if(pdPASS == xTaskCreate(start_task_routine, "start_task", 512U, NULL, 1U, &start_task_handle))
		vTaskStartScheduler();
	else
		return -1;
    
	for( ; ; );
    
    return 0;
}

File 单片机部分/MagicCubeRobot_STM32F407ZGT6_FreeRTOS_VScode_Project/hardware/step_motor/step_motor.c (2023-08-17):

/*!
 * @file: step_motor.c
 * @author: 屠文博-自卓201-201404010126
 * @date: 2023年5月16日21:54:15
 * @brief:  这个文件用于步进电机的驱动.
 *          一共11个步进电机, 脉冲输出引脚使用PF0~PF10, 方向控制引脚使用PG0~PG10.
 *          使用TIM3, 定时器更新中断周期为1.25ms, 即1s中断800次, 即脉冲频率为800Hz. 如果驱动器调节细分至400个脉冲每圈, 则步进电机转速2r/s.
 *          控制步进电机我使用了一个结构体step_motor, 方便一些. 一共控制11个步进电机, 所以定义了一个结构体数组step_motors.
 * 
 * @note:   由于一共使用了11个步进电机, 数量较多, 如果每个都使用定时器来驱动的话, 有点浪费资源, 所以我使用了模拟脉冲(即手动拉高拉低引脚)的方法.
 *          那么也就只需要一个定时器, 11个用于产生脉冲的普通GPIO口即可.
 *          为了尽量减少中断的次数及中断频率, 减少CPU资源无故浪费, 我采用了下面的方法产生脉冲:
 *              进一次中断就产生一个脉冲, 即在中断服务函数中, 先把引脚拉高, 然后卡死延时5us, 再把引脚拉低.
 *          这里的5us是经过示波器和信号发生器测试的, 高电平持续4us以上步进电机驱动器的高速光耦都是能反应得过来的.
 *          另外,
 *          由于一共有11个步进电机, 如果挨个调用库函数拉高拉低引脚, 未免有点太慢太傻了. 所以这里我在处理时使用了编程中的bitmap方式, 即一个数据一共有16bit,
 *          我使用其中的低11bit, 每一位表示一个步进电机. 例如: 第2bit为1, 就表示第2个步进电机需要转动, 即第2个引脚需要产生脉冲.
 *          拉高拉低引脚时使用的也是直接操作寄存器的方法, 速度更快.
 * 
 *          !!>> 控制步进电机这部分我进行了精心设计, 想要转动一个步进电机, 只需要调用void step_motor_run(uint8_t index, uint8_t dir, uint32_t steps);函数即可,
 *          而且也仅仅需要调用这一个函数, 通过参数指定步进电机索引, 转动方向, 转动步数.
 *          而且11个步进电机之间互补相斥, 支持同一时间任意个数的步进电机旋转.
 */

#include "step_motor.h"
#include "bitband.h"
#include "delay.h"
#include "limit.h"
#include "FreeRTOS.h"
#include "task.h"
#include "limit_task.h"


#define NUM_OF_STEPPER_MOTORS   11U //!< 步进电机的数量.
step_motor step_motors[NUM_OF_STEPPER_MOTORS];//!< 定义控制11个步进电机的结构体数组.

volatile uint8_t stepper_rotating = 0U;//!< 有电机在转的标志. 有电机在转为1, 没有电机在转为0. 这个变量主要用于各步进电机之间的同步.


//! 11个步进电机方向控制引脚初始化. 使用PG0~PG10.
static void step_motor_dir_gpio_config(void)
{
    RCC_AHB1PeriphClockCmd(RCC_AHB1Periph_GPIOG, ENABLE);
    
    GPIO_InitTypeDef GPIO_InitStructure;
    GPIO_InitStructure.GPIO_Pin = GPIO_Pin_0 | GPIO_Pin_1 | GPIO_Pin_2 | GPIO_Pin_3 | GPIO_Pin_4 \
                                  | GPIO_Pin_5 | GPIO_Pin_6 | GPIO_Pin_7 | GPIO_Pin_8 | GPIO_Pin_9 | GPIO_Pin_10;
    GPIO_InitStructure.GPIO_Mode = GPIO_Mode_OUT;
    GPIO_InitStructure.GPIO_OType = GPIO_OType_PP;
    GPIO_InitStructure.GPIO_PuPd = GPIO_PuPd_UP;
    GPIO_InitStructure.GPIO_Speed = GPIO_Fast_Speed;
    GPIO_Init(GPIOG, &GPIO_InitStructure);
}


//! 11个步进电机脉冲输出引脚初始化. 使用PF0~PF10.
static void step_motor_pulse_gpio_config(void)
{
    RCC_AHB1PeriphClockCmd(RCC_AHB1Periph_GPIOF, ENABLE);
    
    GPIO_InitTypeDef GPIO_InitStructure;
    GPIO_InitStructure.GPIO_Pin = GPIO_Pin_0 | GPIO_Pin_1 | GPIO_Pin_2 | GPIO_Pin_3 | GPIO_Pin_4 \
                                  | GPIO_Pin_5 | GPIO_Pin_6 | GPIO_Pin_7 | GPIO_Pin_8 | GPIO_Pin_9 | GPIO_Pin_10;
    GPIO_InitStructure.GPIO_Mode = GPIO_Mode_OUT;
    GPIO_InitStructure.GPIO_OType = GPIO_OType_PP;
    GPIO_InitStructure.GPIO_PuPd = GPIO_PuPd_UP;
    GPIO_InitStructure.GPIO_Speed = GPIO_Fast_Speed;
    GPIO_Init(GPIOF, &GPIO_InitStructure);

    for(uint8_t i = 0U; i < 11; i++)//!< 保证初始时刻, 引脚全部为低.
    {
        PFout(i) = 0;
    }
}
    

//! 定时器模式初始化. 仅用于产生更新中断.
static void step_motor_timer3_mode_config(void)
{
    RCC_APB1PeriphClockCmd(RCC_APB1Periph_TIM3, ENABLE);
    
    TIM_TimeBaseInitTypeDef TIM_TimeBaseInitStructure;
    TIM_TimeBaseInitStructure.TIM_Prescaler = 840 - 1;//!< 0.01ms加1.
    TIM_TimeBaseInitStructure.TIM_CounterMode = TIM_CounterMode_Up;
    TIM_TimeBaseInitStructure.TIM_Period = 125 - 1;//!< 周期1.25ms.
    TIM_TimeBaseInitStructure.TIM_ClockDivision = TIM_CKD_DIV1;
    TIM_TimeBaseInitStructure.TIM_RepetitionCounter = 0;
    TIM_TimeBaseInit(TIM3, &TIM_TimeBaseInitStructure);

    NVIC_InitTypeDef NVIC_InitStructure;
	NVIC_InitStructure.NVIC_IRQChannel = TIM3_IRQn;
	NVIC_InitStructure.NVIC_IRQChannelPreemptionPriority = 6;//!< 中断优先级为6, 较高, 可以在中断中使用FreeRTOS的接口.
	NVIC_InitStructure.NVIC_IRQChannelSubPriority = 0;
	NVIC_InitStructure.NVIC_IRQChannelCmd = ENABLE;
    NVIC_Init(&NVIC_InitStructure);

    TIM_ClearITPendingBit(TIM3, TIM_IT_Update);
    TIM_ITConfig(TIM3, TIM_IT_Update, ENABLE);

    TIM_SetCounter(TIM3, 0U);//!< 初始的时候, 先把计数器清0.
}


//! 步进电机结构体中元素的初始化.
static void step_motor_struct_init(void)
{
    for(uint8_t i = 0U; i < 11U; i++)
    {
        step_motors[i].steps = 0U;
        step_motors[i].dir = 0U;
    }
}


//! 总的初始化.
void step_motor_init(void)
{
    step_motor_dir_gpio_config();
    step_motor_pulse_gpio_config();
    step_motor_timer3_mode_config();
    step_motor_struct_init();
}


//! 这个里面就主要是给step和dir赋值.
void step_motor_run(uint8_t index, uint8_t dir, uint32_t steps)
{
    //! 进来先判断一下要转动的是不是导轨, 如果是且导轨已到达限位, 如果还想朝限位走, 则不让走. 如果不会发生危险, 则正常走就行了, 一个if也不会进.
    //! 之所以这样做是为了解决, 当限位开关已经触发的时候, 由于limit_task的检查频率(并非始终在检查, 而是有时间间隔的), 当再次让导轨撞限位时, 还是会撞一点, 的问题.

    if(LIMIT_STATUS(0) == TRIGGER && index == 1U && dir == 1U)//!< 这次调用使导轨0危险, 则本次调用无效.
        return ;

    if(LIMIT_STATUS(1) == TRIGGER && index == 2U && dir == 0U)//!< 或者 这次调用使导轨1危险, 则本次调用无效.
        return ;

    if(LIMIT_STATUS(2) == TRIGGER && index == 4U && dir == 1U)//!< 或者 这次调用使导轨2危险, 则本次调用无效.
        return ;

    if(LIMIT_STATUS(3) == TRIGGER && index == 9U && dir == 1U)//!< 或者 这次调用使导轨3危险, 则本次调用无效.
        return ;


    if((LIMIT_STATUS(0) == TRIGGER && index == 1U && dir == 0) \
        || (LIMIT_STATUS(1) == TRIGGER && index == 2U && dir == 1U) \
        || (LIMIT_STATUS(2) == TRIGGER && index == 4U && dir == 0) \
        || (LIMIT_STATUS(3) == TRIGGER && index == 9U && dir == 0))//!< 如果任何一个要从限位点出发, 那就挂起, 而从其他位置前进不需要挂起.
    {
        vTaskSuspend(limit_task_handle);
    }
    

    if((index == 1U && dir == 1U) \
        || (index == 2U && dir == 0) \
        || (index == 4U && dir == 1U) \
        || (index == 9U && dir == 1U))//!< 如果有任何一个要回去, 就要解挂.
    {
        vTaskResume(limit_task_handle);
    }
    
    //! 其余的就是普通情况了, 常规处理就好.
    step_motors[index].dir = dir;
    step_motors[index].steps = steps;
    
    if(dir == 0U)
        PGout(index) = 0;
    else
        PGout(index) = 1;

    TIM_Cmd(TIM3, ENABLE);
}
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

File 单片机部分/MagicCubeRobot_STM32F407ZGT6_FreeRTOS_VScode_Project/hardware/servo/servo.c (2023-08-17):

/*!
 * @file: servo.c
 * @author: 屠文博-自卓201-201404010126
 * @date: 2023年5月16日21:15:04
 * @brief:  该文件用于驱动舵机的定时器TIM4的初始化, 使用TIM4的CH1, 对应引脚PD12.
 *          这里主要说一下舵机的使用.
 *          舵机要转动需要提供周期为20ms, 高电平持续时间为0.5ms~2.5ms的PWM脉冲, 则0.5ms~2.5ms对应转角为0°~180°.
 *          TIM4频率为84MHz, 我采用了840分频, 所以0.01ms计数器加1, 所以想要20ms的周期, 重装载寄存器值应为2000, 
 *          则产生0.5ms~2.5ms的高电平, 对应的比较寄存器的值应在50~250变化.
 *          之前我设定的重装载值为200, 比较寄存器的值为5~25, 结果发现这样舵机一步就是9°, 太大了, 所以就又扩大了10倍, 使每步变成了0.9°.
 * @note:   我使用信号发生器测试过了, 其实稍微小于0.5ms的脉冲也是可以的. (我想应该是这种舵机精度很低, 结构比较简单, 误差比较大的原因)
 *          在该系统中, 舵机仅需要3个位置, 从下到上记为POS1, POS2, POS3. 我在servol.h中定义了3个宏表示这几个位置对应的比较寄存器的值, 
 *          这3个值分别为47, 153, 236, 是经过测试的. 如果后期因为某些原因对不齐时, 可以自己在servo.h中调整这几个值.
 */

#include "servo.h"
#include "stm32f4xx.h"


//! TIM4, CH1, PD12
static void timer4_gpio_config(void)
{
    RCC_AHB1PeriphClockCmd(RCC_AHB1Periph_GPIOD, ENABLE);
    
    GPIO_InitTypeDef GPIO_InitStructure;
    GPIO_InitStructure.GPIO_Pin = GPIO_Pin_12;
    GPIO_InitStructure.GPIO_Mode = GPIO_Mode_AF;
    GPIO_InitStructure.GPIO_OType = GPIO_OType_PP;
    GPIO_InitStructure.GPIO_PuPd = GPIO_PuPd_UP;
    GPIO_InitStructure.GPIO_Speed = GPIO_Fast_Speed;
    
    GPIO_PinAFConfig(GPIOD, GPIO_PinSource12, GPIO_AF_TIM4);
    
    GPIO_Init(GPIOD, &GPIO_InitStructure);
}
    
 
static void timer4_mode_config(void)
{
    RCC_APB1PeriphClockCmd(RCC_APB1Periph_TIM4, ENABLE);
    
    TIM_TimeBaseInitTypeDef TIM_TimeBaseInitStructure;
    TIM_TimeBaseInitStructure.TIM_Prescaler = 840 - 1;//!< 0.01ms加1.
    TIM_TimeBaseInitStructure.TIM_CounterMode = TIM_CounterMode_Up;
    TIM_TimeBaseInitStructure.TIM_Period = 2000 - 1;//!< 计数周期20ms. (则高电平持续时间对应的pulse为50~250)
    TIM_TimeBaseInitStructure.TIM_ClockDivision = TIM_CKD_DIV1;
    TIM_TimeBaseInitStructure.TIM_RepetitionCounter = 0;
    TIM_TimeBaseInit(TIM4, &TIM_TimeBaseInitStructure);
    
    TIM_OCInitTypeDef TIM_OCInitStructure;
    TIM_OCInitStructure.TIM_OCMode = TIM_OCMode_PWM1;
    TIM_OCInitStructure.TIM_OutputState = TIM_OutputState_Enable;
    TIM_OCInitStructure.TIM_OutputNState = TIM_OutputNState_Disable;
    TIM_OCInitStructure.TIM_Pulse = POS_1_PULSE;//!< 初始时刻在下面.
    TIM_OCInitStructure.TIM_OCPolarity = TIM_OCPolarity_High;
    TIM_OCInitStructure.TIM_OCNPolarity = TIM_OCNPolarity_High;
    TIM_OCInitStructure.TIM_OCIdleState = TIM_OCIdleState_Set;
    TIM_OCInitStructure.TIM_OCNIdleState = TIM_OCNIdleState_Set;
    TIM_OC1Init(TIM4, &TIM_OCInitStructure);

    TIM_Cmd(TIM4, ENABLE);
    TIM_CtrlPWMOutputs(TIM4, ENABLE);
}


void servo_init(void)
{
    timer4_gpio_config();
    timer4_mode_config();
}

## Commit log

2023-08-17 第一次提交, 要上传到github
    [35mm铜柱.SLDPRT, 42步进电机.SLDPRT, 42步进电机同步轮.SLDPRT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]
2023-08-17 完善了README.md
2023-08-21 改正了README.md的格式问题
2023-08-21 README.md数学公式渲染问题
